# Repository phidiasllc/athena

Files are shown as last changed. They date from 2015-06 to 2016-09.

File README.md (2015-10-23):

<h1>Athena is a robot that makes lots of things</h1>
<p> Athena is derived from the <a href="https://github.com/mtu-most/most-delta">MOST Delta RepRap 3D printer</a>, which was derived from the <a href="http://www.thingiverse.com/thing:17175">Rostock RepRap 3-D Printer</a>.

<h2>SCAD files now available</h2>
In order to use the OpenSCAD files, copy them into a folder along with all of the scad files in the <a href="https://github.com/phidiasllc/scad_libraries">scad_libraries</a> repository. Render parts or plates using athena_renderer.scad.

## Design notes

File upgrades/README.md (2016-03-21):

<h1>Installing Upgrades</h1>
Upgrading requires a USB thumbdrive:
<ol>
<li>Connect a USB thumbdrive to your computer</li>
<li>Download the file(s) to install to the root of your thumbdrive.</li>
<ol>
<li>Click on the desired file in the above list</li>
<li>In right-click the button labled "Raw" in the page and select "Save link as..."</li>
<li>navigate to the location you wish to store the file</li>
</ol>
<li>Remove the thumbdrive from your computer (Eject/unmount first!)</li>
<li>Shutdown the printer and unplug power</li>
<li>Insert the thumbdrive with the downloaded files on it into the USB socket on the printer</li>
<li>Restore power to the printer</li>
<li>The beaglebone should boot, run the script and then power back down</li>
<li>After the Beaglebone has booted and then shut back down, unplug power from the printer and remove the USB thumbdrive from the USB socket in the printer</li>
<li>Restore printer power</li>
</ol>

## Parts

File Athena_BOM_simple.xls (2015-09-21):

Function | Type | Item | Count | Length | Purpose
Motor end | fastener | M3×12 socket head cap screw | 12 |  | mounting motor
Motor end | fastener | M3 washer | 18 |  | mounting motor and bar clamp
Motor end | electronic | NEMA17 motor | 3 |  | motor
Motor end | printed | Motor end | 3 |  | apex
Motor end | printed | Bar Clamp | 6 |  | clamping guide rods
Motor end | fastener | M3×16 socket head cap screw | 6 |  | Bar clamp
Motor end | fastener | M3 nut | 6 |  | Bar clamp
Motor end | fastener | #6×¾" sheet metal screw | 24 |  | apex to linking board and base
Motor end | misc | 16 tooth GT2 pulley | 3 |  | pulley
Motor end | fastener | M3×6 set screw | 6 |  | pulley set screw
Idler end | printed | Idler end | 3
Idler end | bearing | 608ZZ bearing | 6 |  | belt idler
Idler end | fastener | M8×40 hex head cap screw | 3 |  | idler shaft
Idler end | fastener | M8 nut | 3 |  | idler shaft
Idler end | fastener | M8 washer | 9 |  | idler shaft
Idler end | printed | Bar Clamp | 6 |  | clamping guide rods
Idler end | fastener | M3×16 socket head cap screw | 6 |  | Bar clamp
Idler end | fastener | M3 nut | 6 |  | Bar clamp
Idler end | fastener | M3 washer | 6 |  | Bar clamp
Idler end | fastener | #6×¾" sheet metal screw | 24 |  | apex to linking board and top
Carriages + Effector | printed | Simple Carriage | 3
Carriages + Effector | printed | Print Effector | 1
Carriages + Effector | misc | ⅜"×⅛" Counter sunk ring magnet N52 | 12
Carriages + Effector | fastener | M3×12 socket head cap screw | 3 |  | limit switch engage adjust
Carriages + Effector | fastener | M3×16 socket head cap screw | 3 |  | belt terminator
Carriages + Effector | fastener | M3 nut | 3 |  | belt terminator
Carriages + Effector | fastener | M3 washer | 3 |  | belt terminator
Carriages + Effector | printed | Fixed belt terminator | 3
Carriages + Effector | printed | Free belt terminator | 3
Carriages + Effector | misc | Small wire tie | 12 |  | bearings on carriage, belt behind terminator
Carriages + Effector | misc | Large wire tie | 3 |  | belt terminator
Carriages + Effector | misc | 6mm GT2 belt, 1500mm | 3 | 1500
Carriages + Effector | bearing | ⅜" G25 ball bearing | 12 |  | tie rod ends
Carriages + Effector | misc | 0.25"od 0.014" wall thickness 242mm aluminum rod | 6 |  | tie rods
Carriages + Effector | bearing | LM8UU linear bearing | 6 |  | Carriage
Carriages + Effector | electronic | J-head hot end (incl. 100kΩ thermistor and 5.6Ω resistor) | 1
Carriages + Effector | electronic | 40 mm fan | 1
Carriages + Effector | fastener | M3×12 socket head cap screw | 2 |  | Fan
Carriages + Effector | fastener | 4mm pneumatic quick release, drilled | 1 |  | hot end quick release
Carriages + Effector | electronic | 18ga Speaker wire, 1500mm | 1 | 1500 | heating power
Carriages + Effector | electronic | Twisted pair wire, 1500mm | 2 | 1500 | Fan and thermistor
Frame | misc | 38×210×12mm plywood | 3 |  | top linking boards
Frame | misc | 38×240×12mm plywood | 3 |  | bottom linking boards
Frame | misc | Hexagonal plywood donut | 1 |  | top
Frame | misc | Hexagonal base | 1 |  | bottom
Frame | misc | 60×605×12mm plywood | 3 |  | vertical boards (only 2 for fixed tool mount)
Frame | bearing | 8mm diameter A2 tool steel, 590mm | 6 | 590 | guide rods
Frame | fastener | M3×50 socket head cap screw | 12 |  | vertical board to apex (only 8 for fixed tool mount)
Frame | fastener | M3 nut | 12 |  | vertical board to apex (only 8 for fixed tool mount)
Frame | fastener | M3 washer | 24 |  | vertical board to apex
Electronics | fastener | M2×12 socket head cap screw | 6 |  | top limit switch
Electronics | fastener | M2 washer | 6 |  | top limit switch
Electronics | electronic | Lever action limit switch | 3 |  | top apex
Electronics | electronic | Twisted pair wire, 1500mm | 3 | 1500 | top limit switches
Electronics | electronic | Melzi controller | 1
Electronics | electronic | Beaglebone Black | 1
Electronics | printed | Electronics mount 1 | 1
Electronics | printed | Electronics mount 2 | 1
Electronics | fastener | M3×6 socket head cap screw | 7 |  | Electronics mounting
Electronics | fastener | #6×½" sheet metal screw | 3 |  | electronics mount
Electronics | electronic | rj45 extension | 1 |  | Extend BBB network connection
Electronics | electronic | USB extension | 1 |  | Extend BBB USB connection
Electronics | printed | Socket Panel | 1 |  | Panel for electrical connectors
Electronics | electronic | 5×2.5mm barrel connector | 1 |  | power input
Electronics | electronic | 18ga Speaker wire, 250mm | 1 | 250 | power input
Electronics | electronic | 18ga Speaker wire, 100mm | 1 | 100 | power input
Electronics | electronic | Melzi to beaglebone bridge board | 1 |  | BBB power
Electronics | electronic | USB cable A to mini B | 1 |  | melzi
Electronics | electronic | Heatshrink tubing | 2
Electronics | electronic | 12V 5/6A power supply | 1 |  | power
Electronics | fastener | M3×6 socket head cap screw | 2 |  | rj45 extension cord mount
Extruder drive | electronic | NEMA17 motor | 1 |  | Cold end drive
Extruder drive | misc | MK7 drive gear | 1 |  | Cold end drive
Extruder drive | fastener | M3×6 set screw | 1 |  | Drive gear
Extruder drive | bearing | MR105Z roller bearing | 1 |  | cold end shaft
Extruder drive | bearing | 608ZZ bearing | 1 |  | Cold end preload idler
Extruder drive | fastener | M3×6 socket head cap screw | 1 |  | motor mount
Extruder drive | fastener | M3×25 socket head cap screw | 1 |  | motor mount
Extruder drive | fastener | M3×30 socket head cap screw | 2 |  | motor mount
Extruder drive | misc | ¼" fuel line, 25mm | 1 | 25 | idler spring
Extruder drive | fastener | M3×45 socket head cap screw | 2 |  | idler preload
Extruder drive | fastener | M3 nut | 2 |  | idler preload
Extruder drive | fastener | M3 washer | 2 |  | idler preload
Extruder drive | fastener | #6×½" sheet metal screw | 2 |  | cold end mount
Extruder drive | misc | 2mm id 4mm od PTFE tube, 630mm | 1 | 630 | bowden sheath
Extruder drive | misc | 2mm id 4mm od PTFE tube, 40mm | 1 | 40 | infeed
Extruder drive | printed | Extruder drive body | 1 |  | cold end
Extruder drive | printed | Extruder linking bar | 1 |  | cold end
Extruder drive | printed | Extruder preload idler housing | 1 |  | cold end
Extruder drive | printed | Extruder preload idler shaft | 1 |  | cold end
Extruder drive | fastener | 4mm pneumatic quick release | 1 |  | Bowden sheath retainer
Frame | printed | Spool holder pivot | 1 |  | spool holder
Frame | printed | Spool holder arm | 1 |  | spool holder
Frame | printed | Spool holder arm retainer | 1 |  | spool holder
Frame | fastener | #6×½" sheet metal screw | 2 |  | spool holder
Frame | fastener | M3×12 socket head cap screw | 1 |  | spool holder pivot
Frame | printed | glass hold down | 3 |  | securing glass
Frame | fastener | #6×½" sheet metal screw | 3 |  | securing glass
Frame | misc | 300mm diameter glass build platform | 1

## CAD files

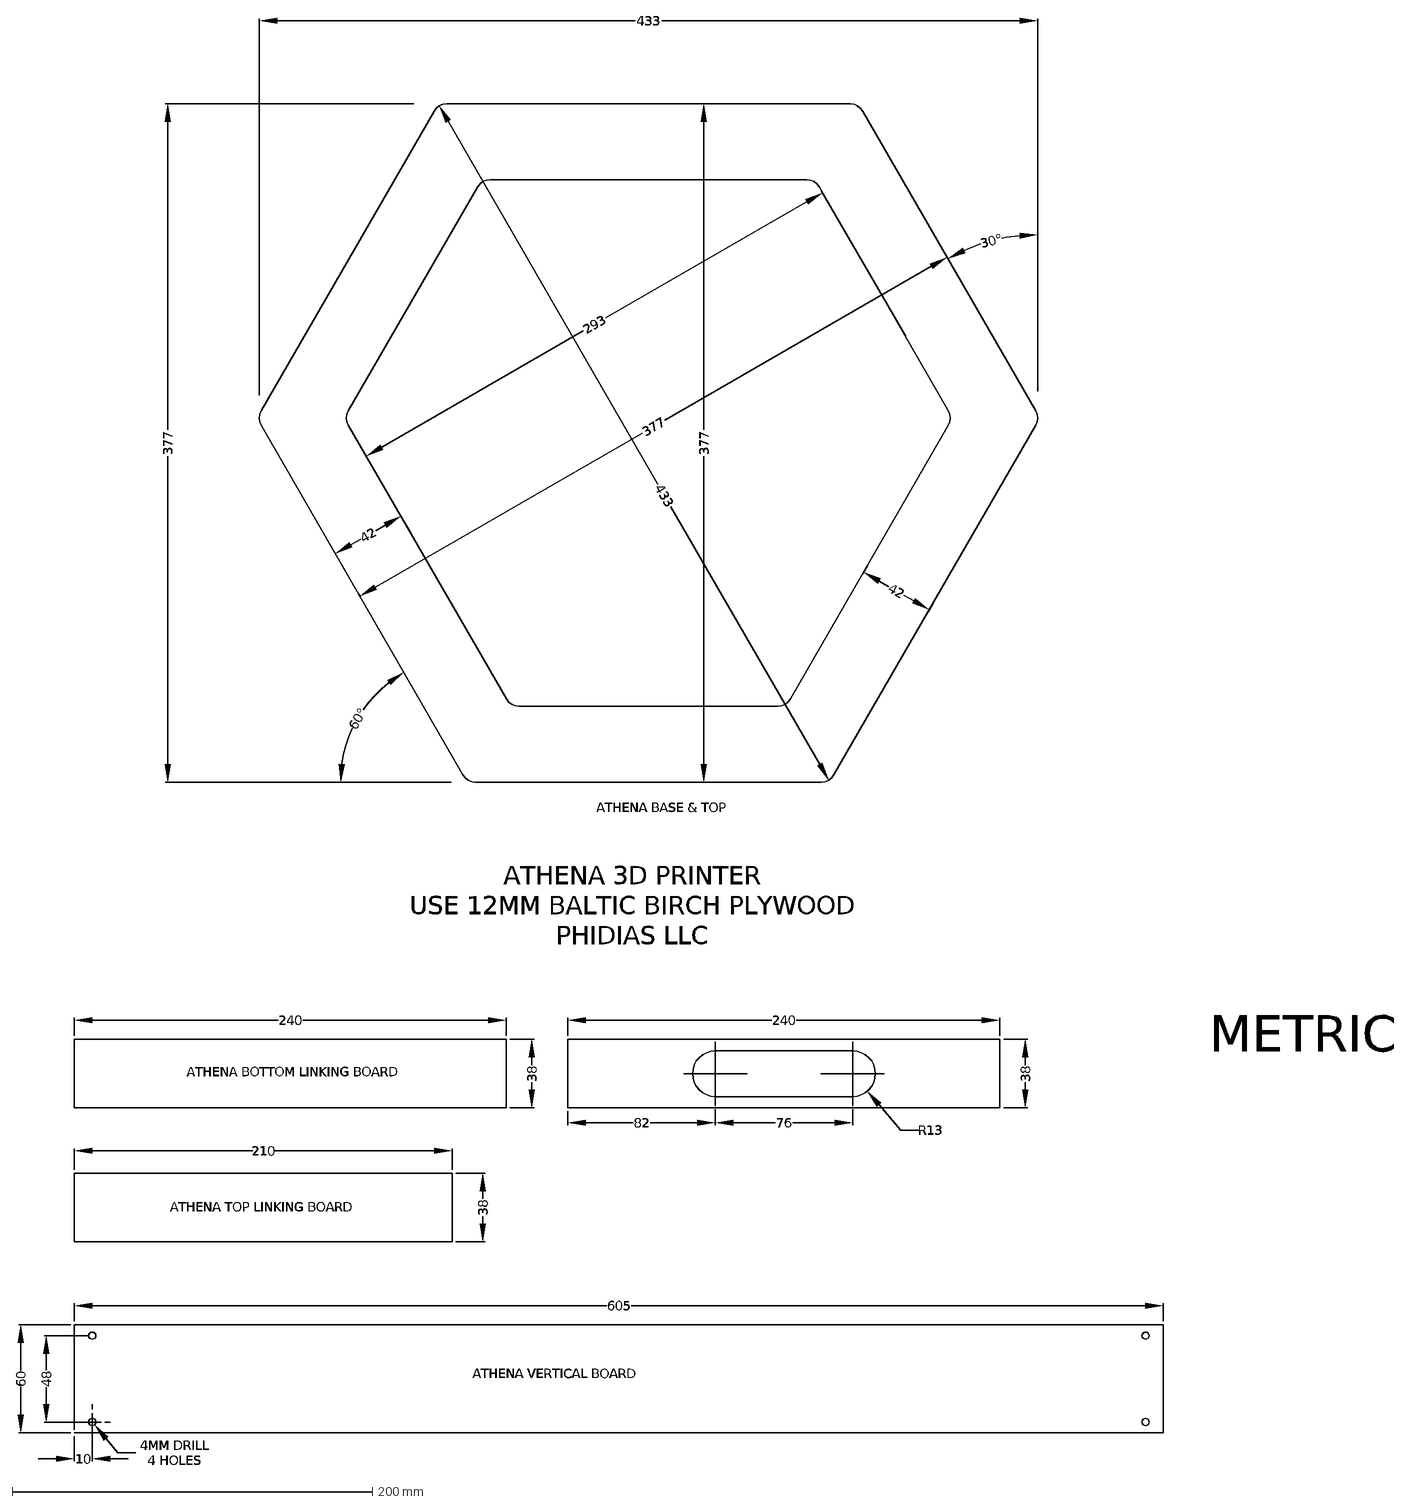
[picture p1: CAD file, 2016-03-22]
cad/ATHENA WOOD PARTS.dxf
ATHENA BOTTOM LINKING BOARD
240
38
210
ATHENA TOP LINKING BOARD
605
ATHENA VERTICAL BOARD
377
433
ATHENA BASE & TOP
42
293
82
76
R13
60
10
48
4MM DRILL 4 HOLES
60°
30°
METRIC
ATHENA 3D PRINTER USE 12MM BALTIC BIRCH PLYWOOD PHIDIAS LLC

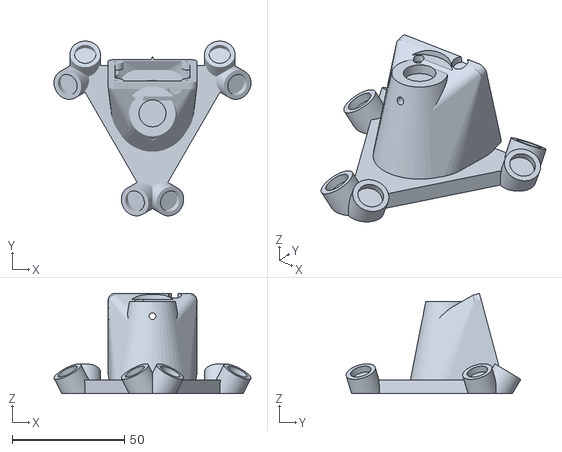
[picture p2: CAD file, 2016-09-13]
stl/hotend_effector.stl
87.9 x 77.9 x 44.7

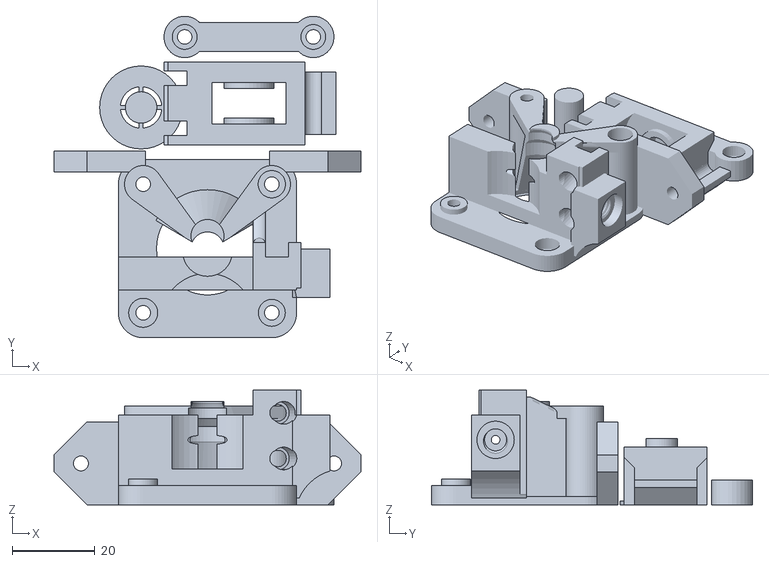
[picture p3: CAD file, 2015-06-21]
stl/extruder_drive_quickrelease.stl
74.0 x 77.5 x 27.7

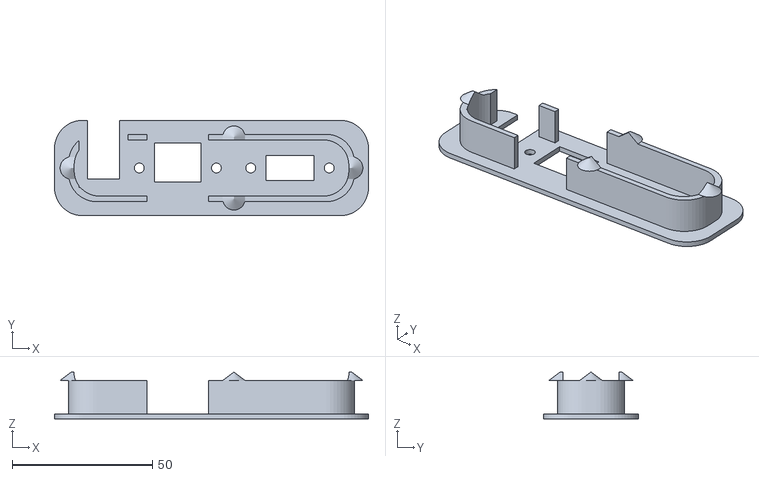
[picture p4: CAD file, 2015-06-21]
stl/connector_plate.stl
112.0 x 34.0 x 16.8

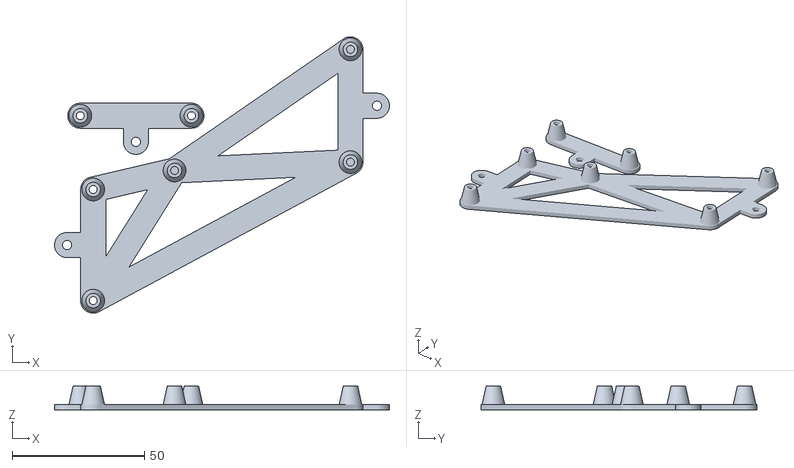
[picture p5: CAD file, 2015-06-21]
stl/electronics_mounts.stl
126.6 x 104.5 x 9.00

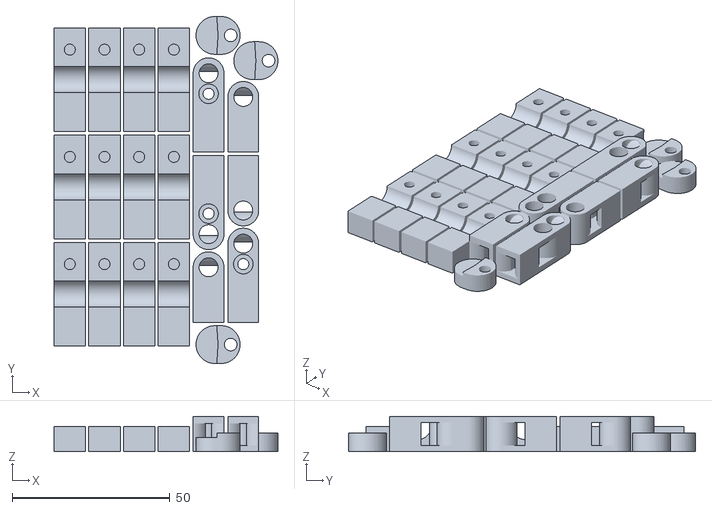
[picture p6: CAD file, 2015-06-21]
stl/bar_clamps_terms_glass_holddowns.stl
71.0 x 110.0 x 11.2

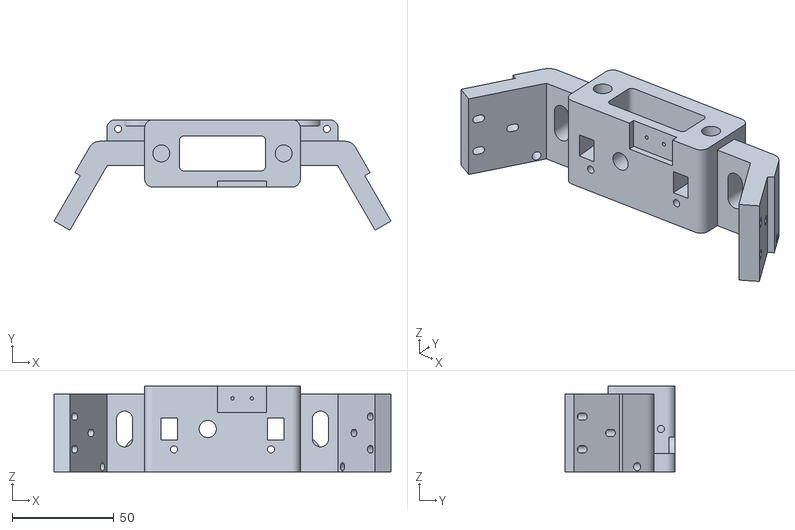
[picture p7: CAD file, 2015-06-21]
stl/end_idler.stl
165.2 x 54.1 x 42.0

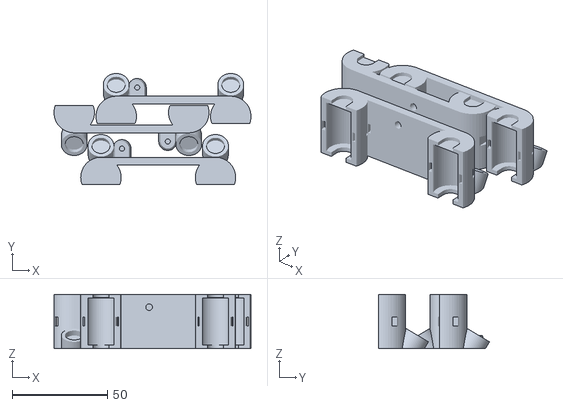
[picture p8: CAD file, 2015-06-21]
stl/simple_carriages.stl
103.2 x 58.2 x 28.5

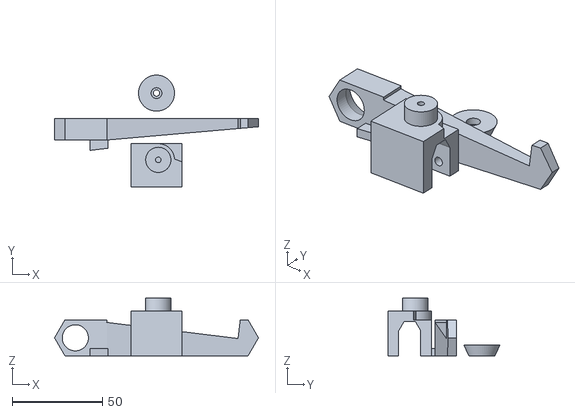
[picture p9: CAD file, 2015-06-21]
stl/spool_holder_wood.stl
113.1 x 62.0 x 32.0

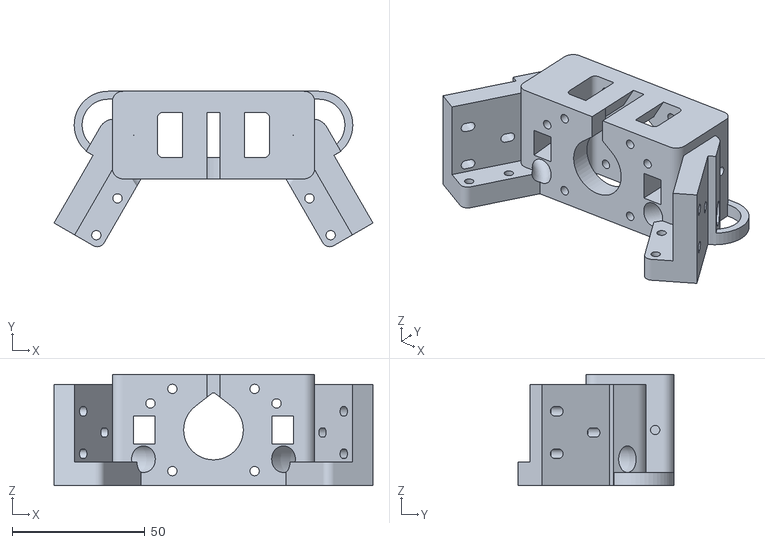
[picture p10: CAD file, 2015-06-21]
stl/end_motor.stl
120.2 x 58.6 x 42.0

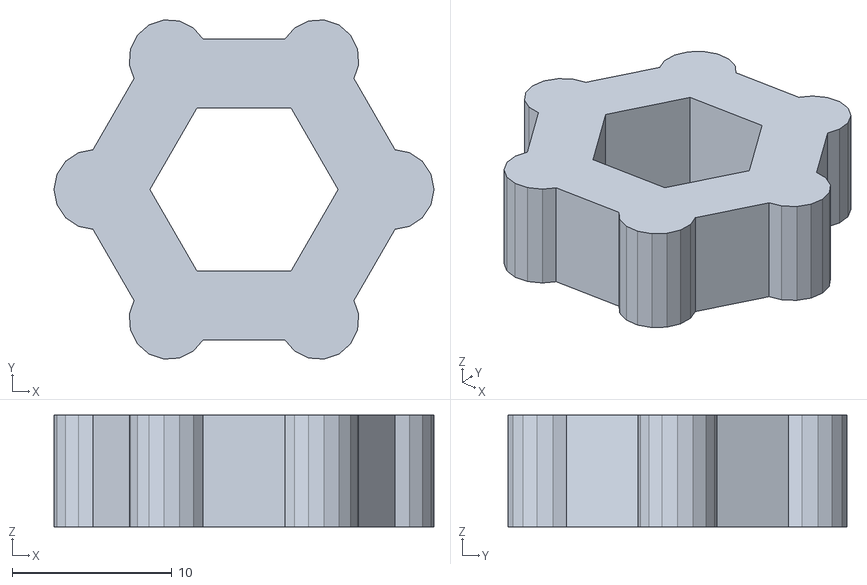
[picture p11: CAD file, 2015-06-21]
stl/thumbscrew.stl
23.8 x 21.2 x 7.00

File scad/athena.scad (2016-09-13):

/************************************************************************************

athena.scad - structural and tool objects required to build an Athena delta platform
Copyright 2015 Jerry Anzalone
Author: Jerry Anzalone <info@phidiasllc.com>

This program is free software: you can redistribute it and/or modify
it under the terms of the GNU Affero General Public License as
published by the Free Software Foundation, either version 3 of the
License, or (at your option) any later version.

This program is distributed in the hope that it will be useful,
but WITHOUT ANY WARRANTY; without even the implied warranty of
MERCHANTABILITY or FITNESS FOR A PARTICULAR PURPOSE. See the
GNU Affero General Public License for more details.

You should have received a copy of the GNU Affero General Public License
along with this program. If not, see <http://www.gnu.org/licenses/>.

************************************************************************************/

// requires the common delta modules
include <simple_delta_common.scad>

/************  layer_height is important - set it to the intended print layer height  ************/
layer_height = 0.33; // layer height that the print will be produced with

// Bowden sheath dims
d_175_sheath = 4.8;
175_bowden = [d_M4_nut, h_M4_nut, d_175_sheath];
d_300_sheath = 6.55;
300_bowden = [d_M6_nut, h_M6_nut, d_300_sheath];

bowden = 175_bowden; // set to the diameter of the Bowden sheath desired, defined above

echo_dims = false; // set to true to echo pertinent dimensions - will repeat some

// [w, l, t] = [y, x, z]
$fn = 48;
pi = 3.1415926535897932384626433832795;

// bar clamp dims
t_bar_clamp = 8;
h_bar_clamp = 10;

// the following sets the spacing of the linking board mounts on motor/idler ends
cc_idler_mounts = 120; // c-c of mounts on idler end - large to maximize x-y translation when in fixed tool mode and minimizes material use for bases
cc_motor_mounts = 75; // c-c of mounts on idler end

// printer dims
r_printer = 175; // radius of the printer, distance from printer center to guide rod centers - typically 175
l_tie_rod = 250; // length of the tie rods - typically 250
l_guide_rods = 595; // length of the guide rods - only used for assembly

// belt, pulley and idler dims
idler = bearing_608;
w_belt = 6; // width of the belt (not used)
pulley_cogs = 16; // number of cogs on the pulley
belt = GT2; // the type of drive belt to be used
h_idler_washer = h_M8_washer; // idler bearing shaft washer
d_idler_shaft_head = d_M8_nut; // idler bearing shaft head diameter
h_idler_shaft_head = h_M8_nut; // idler bearing shaft head height - sets nut pocket depth

// the diameter of the pulley isn't the whole story - the belt rides on the pulley at it's root radius
// but on the idler bearing, it rides on the tips of the cogs, pushing its pitch radius outwards
od_idler = idler[0]; // idler OD
id_idler = idler[1]; // idler id
h_idler = h_608; // thickness of idler
n_idlers = 2; // number of idler bearings
d_pulley = pulley_cogs * belt[0] / pi - (belt[1] - belt[2]); // diameter of the pulley (used to center idler)
offset_idler = (od_idler - d_pulley) / 2 + belt[2]; // amount to offset idler bearing so belt stays parallel with guide rods

// guide rod and clamp dims
cc_guides = 60; // center-to-center of the guide rods
d_guides = 8.3; // diameter of the guide rods - a little big for clearance
pad_clamp = 8; // additional material around guide rods
gap_clamp = 2; // opening for clamp

// following for tabs on either side of clamp to which linking boards are attached
// the radius of the delta measured from the center of the guide rods to the center of the triangle
// as drawn here, the tangent is parallel to the x-axis and the guide rod centers lie on y=0
//cc_mount = 75; // center to center distance of linking board mount pivot points standard = 75
h_apex = 1.5 * 25.4; // height of the portion of motor and idler ends mating with linking board
w_mount = 12; // thickness of the tabs the boards making up the triangle sides will attach to
l_mount = 40; // length of said tabs
cc_mount_holes = 16;
l_base_mount = l_mount;
w_base_mount = 14.1;
t_base_mount = 9.0;
r_base_mount = 3;
l_mount_slot = 2; // length of the slot for mounting screw holes

cc_v_board_mounts = 2 * (cc_guides / 2 - pad_clamp + d_M3_screw / 2); // c-c mounts for vertical boards

l_idler_relief = cc_guides - d_guides - pad_clamp - 1.5; // with guide rod clamp design, the length needs to be smaller so there are walls for bridging
w_idler_relief = n_idlers * h_idler + 2 * h_idler_washer;
r_idler_relief = 2; // radius of the relief inside the apex
l_clamp = cc_guides + d_guides + pad_clamp;
w_clamp = w_idler_relief + pad_clamp + 8;
h_clamp = l_NEMA17;

// magnetic ball joint dims
d_ball_bearing = 3 * 25.4 / 8;
id_magnet = 15 * 25.4 / 64;
od_magnet = 3 * 25.4 / 8;
h_magnet = 25.4 / 8;
r_bearing_seated = pow(pow(d_ball_bearing / 2, 2) - pow(id_magnet / 2, 2), 0.5); // depth ball bearing sinks into magnet id
h_carriage_magnet_mount = 9;
h_effector_magnet_mount = 10;
r_pad_carriage_magnet_mount = 2;
r_pad_effector_magnet_mount = 2;

// effector dims
// l_effector needs to be played with to keep the fan from hitting the tie rods
l_effector = 60; // cc of tie rod bearings on effector
h_effector = equilateral_height_from_base(l_effector);
r_effector = l_effector * tan(30) / 2 + 11; // radius of the magnet mounts
t_effector = 6; // thickness of the effector base
h_triangle_inner = h_effector + 12;
r_triangle_middle = equilateral_base_from_height(h_triangle_inner) * tan(30) / 2;

// for the small tool end effector:
d_small_effector_tool_mount = 30; // diameter of the opening in the end effector that the tool will pass through
d_small_effector_tool_magnet_mount = 1 + d_small_effector_tool_mount + od_magnet + 2 * r_pad_effector_magnet_mount; // ring diameter of the effector tool magnet mounts

// for the large tool end effector:
d_large_effector_tool_mount = 50;
d_large_effector_tool_magnet_mount = h_triangle_inner;

// Bowden sheath quick release fitting dims
d_quickrelease_threads = 6.4; // M6 threads, but this gives best fit
l_quickrelease_threads = 5; // length of threads on quick release
pitch_quickrelease_threads = 1;
d_quickrelease = 12; // diameter of the hex portion for counter-sinking quick release into hot end tool
countersink_quickrelease = 6; // depth to contersink quick release fitting into hot end tool when not headless

// hot end dims
pad_jhead = 8; // this is added to the diameter of the cage to permit clearance for the hotend
pad_e3d = 14;
t_hotend_cage = t_heat_x_jhead - h_groove_jhead - h_groove_offset_jhead;
d_hotend_side = d_large_jhead + pad_jhead;
z_offset_retainer = t_hotend_cage - t_effector / 2 - 3;  // need an additional 3mm to clear the interior of the cage
a_fan_mount = 15;
l_fan = 39.5;
r_flare = 6;
h_retainer_body = h_groove_jhead + h_groove_offset_jhead + 4;
r1_retainer_body = d_hotend_side / 2 + r_flare * 3 / t_hotend_cage;
r2_retainer_body = r1_retainer_body - r_flare * h_retainer_body / t_hotend_cage;
r2_opening = (d_hotend_side - 5 ) / 2 + r_flare * (t_hotend_cage - 6 - t_effector + 3.0) / (t_hotend_cage - 6);//r1_opening - r_flare * (t_effector + 1.5) / t_hotend_cage;
r1_opening = r2_opening - 1.5;
d_retainer_screw = d_M2_screw;

// carriage dims:
w_carriage_web = 4;
h_carriage = l_lm8uu + 4;
carriage_offset = 18.6; // distance from center of guide rods to center of ball mount pivot
y_web = - od_lm8uu / 2 - (3 - w_carriage_web / 2);
stage_mount_pad = 2.2;

// limit switch dims
l_limit_switch = 24;
w_limit_switch = 6;
t_limit_switch = 14;
cc_limit_mounts = 9.5;
limit_x_offset = 11; // 11 places limit switch at guide rod, otherwise center at cc_guides / 2 - 8
limit_y_offset = d_M3_screw - carriage_offset;

// center-to-center of tie rod pivots
tie_rod_angle = acos((r_printer - r_effector - carriage_offset) / l_tie_rod);

// tool mount member dims
w_member = 25.4; // narrow dimension of member
l_member = 3 * 25.4; // wide dimension of member

// aluminum member dims
l_vertical_board = 3 * 25.4; // long dimension of rectangular tube making vertical board
w_vertical_board = 25.4; // short dimention of rectangular tube making vertical board
l_linking_board = 38.6;
w_linking_board = 3 * 25.4 / 4;

// BBB dims; origin at corner w/ power jack, starting from hole nearest power jack, going counter clockwise
bbb_hole0 = [14.61, 3.18];
bbb_hole1 = [14.61 + 66.5, 6.35];
bbb_hole2 = [14.61 + 66.5, 6.35 + 42.6];
bbb_hole3 = [14.61, 3.18 + 48.39];
bbb_holes = [bbb_hole0, bbb_hole1, bbb_hole2, bbb_hole3];
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

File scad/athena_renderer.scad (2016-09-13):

/************************************************************************************

athena_renderer.scad - easily select and render parts and plates for manufacture of Athena platform
Copyright 2015 Jerry Anzalone
Author: Jerry Anzalone <info@phidiasllc.com>

This program is free software: you can redistribute it and/or modify
it under the terms of the GNU Affero General Public License as
published by the Free Software Foundation, either version 3 of the
License, or (at your option) any later version.

This program is distributed in the hope that it will be useful,
but WITHOUT ANY WARRANTY; without even the implied warranty of
MERCHANTABILITY or FITNESS FOR A PARTICULAR PURPOSE. See the
GNU Affero General Public License for more details.

You should have received a copy of the GNU Affero General Public License
along with this program. If not, see <http://www.gnu.org/licenses/>.

************************************************************************************/

// include the modules required for rendering
include <athena.scad>

render_part(part_to_render = 14);
//render_plate(plate_to_render = 1);

// renders individual parts
module render_part(part_to_render) {
	// end that holds motor - 3 required
	if (part_to_render == 1) athena_end_idler(z_offset_guides = 8);

	// end that holds idler bearings and end limit switches - 3 required
	if (part_to_render == 2) athena_end_motor(z_offset_guides = 8);

	// clamps the guide rods firmly to motor/idler ends - 12 required
	if (part_to_render == 3) bar_clamp();

	// permits tensioning of belts and mount point to carriage - 3 sets required
	if (part_to_render == 4) athena_belt_terminators();

	// carriages ride on the guide rods 3 required for basic platform
	if (part_to_render == 5) athena_basic_carriage();

	// carriages ride on the guide rods 3 required for Parthenos
	if (part_to_render == 6) athena_convertible_carriage(linear_bearing = bearing_lm8uu);

	// the roller switch mount - 3 required for Parthenos
	if (part_to_render == 7) central_limit_switch();

	// if the platform uses a BBB and melzi, one of these is required
	if (part_to_render == 8) bbb_melzi_mount(render_large = true, render_small = true);

	// mounts to vertical board, holds magnetic tools not in use and hides wires - convenience, not required for Parthenos
	if (part_to_render == 9) athena_tool_holder();

	// mounts to vertical board to which extruder drive is mounted and holds spool - convenience, not required
	if (part_to_render == 10) athena_spool_holder(render_mount = true, render_holder = false
	, mount_wood = true);

	// mounts to vertical board, holds tools and hides wires - convenience, not required
	if (part_to_render == 11) athena_hand_tool_holder(wood_mount = true, sonicare_magnet = false);

	// Mounting plate fits in slotted motor-end linking board, one required; print with support
	if (part_to_render == 12) connector_plate();

	// for holding glass to base plate, three required
	if (part_to_render == 13) glass_holddown();

	// end effector with built-in mount for hot end, one required for basic platform
	if (part_to_render == 14) hotend_effector(headless = true, quickrelease = true, vent = false, dalekify = false);

	// thumbscrew for the quick release connector
	if (part_to_render == 15) thumbscrew_quickrelease();

	// shroud mounted to bottom of end effector for improved print cooling
	if (part_to_render == 16) hotend_shroud(height = 18, twist = 5);

	// a place to play
	if (part_to_render == 99) sandbox();
}

// renders production plates
module render_plate(plate_to_render) {
	// approximate build circle to assure placement and fit on build platform
//	color([1, 0, 0])
//		circle(r = 125);

	if (plate_to_render == 1)
		for (i = [-1:1])
			translate([0, i * (w_clamp + 2) + 20, 0])
				athena_end_idler(z_offset_guides = 8);

	if (plate_to_render == 2) {
		translate([0, -w_clamp / 2 - 6, 0])
			athena_end_motor();

		translate([0, w_clamp / 2 + 6, 0])
			rotate([0, 0, 180])
				athena_end_motor();

		translate([l_clamp - 6, 0, 0])
			rotate([0, 0, 90])
				athena_end_motor();
	}

	// hot end effector
	if (plate_to_render == 3) {
		hotend_effector(quickrelease = true, dalekify = false);
	}

	// fixed terminators
	if (plate_to_render == 4) {
		for (i = [-3:2], j = [-1:1])
			//rotate([0, 0, i * 120])
				translate([i * 11, j * 32, 0])
					athena_fixed_belt_terminator();
	}

	// free terminators
	if (plate_to_render == 5) {
		for (i = [-3:2], j = [-1:1])
			//rotate([0, 0, i * 120])
				translate([i * 11, j * 25, 0])
					athena_free_belt_terminator();
	}

	// bar clamps
	if (plate_to_render == 6) {
		translate([-h_bar_clamp / 2 - 6, -w_clamp - 1, t_bar_clamp / 2])
			for (i = [0:2])
				for (j = [-4:3])
					translate([j * -(h_bar_clamp + 1), i * (w_clamp + 1), 0])
						bar_clamp();
	}

	if (plate_to_render == 7) {
		// Parthenos carriages
		translate([22, -2, 0])
			rotate([0, 0, 180])
				athena_convertible_carriage();

		athena_convertible_carriage();

		translate([14, -39, 0])
			rotate([0, 0, 180])
				athena_convertible_carriage();
	}

	if (plate_to_render == 8) {
		translate([22, -2, 0])
			rotate([0, 0, 180])
				athena_basic_carriage();

		athena_basic_carriage();

		translate([14, -34, 0])
			rotate([0, 0, 180])
				athena_basic_carriage();
	}

	if (plate_to_render == 9) {
		for (i = [-1:1], j = [-2:1])
			translate([i * 19, j * 22 + ((i == 0) ? 11 : 0), 0])
				thumbscrew_quickrelease();
	}

	if (plate_to_render == 10) {
		for (i = [-1:1], j = [-1,0])
			translate([i * 30, j * 25 + 12.5, 0])
			athena_spool_holder(
				render_mount = true,
				render_holder = false,
				mount_wood = true);
	}

	if (plate_to_render == 11) {
		for(i = [-1:1])
			translate([0, i * 55, 0])
				bbb_melzi_mount(render_large = true, render_small = false);

	}
}

module sandbox() {
	linear_bearing = bearing_lm8uu;
	spacing = 0.5;
	union() {
		translate([0, 0, -h_carriage / 2 + spacing])
			difference() {
				union() {
					carriage_body(linear_bearing = linear_bearing);

					// magnet mounts
					for (i = [-1, 1])
						translate([i * l_effector / 2, -carriage_offset, stage_mount_pad + h_carriage_magnet_mount / sin(tie_rod_angle)])
							rotate([90 - tie_rod_angle, 0, 0])
								magnet_mount(r_pad = r_pad_carriage_magnet_mount, h_pad = h_carriage_magnet_mount);

					mirror([0, 0, 1])
						for (i = [-1, 1])
							translate([i * l_effector / 2, -carriage_offset, stage_mount_pad + h_carriage_magnet_mount / sin(tie_rod_angle)])
								rotate([90 - tie_rod_angle, 0, 0]) {
									magnet_mount(r_pad = r_pad_carriage_magnet_mount, h_pad = h_carriage_magnet_mount);

									// support for printing the mounts
									translate([0, 0, (h_magnet + h_carriage_magnet_mount) / 2 - r_bearing_seated + 0.25])
										difference() {
											cylinder(r = od_magnet / 2 + r_pad_carriage_magnet_mount, h = h_magnet + h_carriage_magnet_mount, center = true);

											cylinder(r = od_magnet / 2, h = h_magnet + h_carriage_magnet_mount, center = true);
										}
							}

				}

				for (i = [-1, 1])
					translate([i * cc_guides / 2, 0, 0])
						carriage_wire_tie_relief(
							linear_bearing = linear_bearing,
							clearance = 0.5
						);

				carriage_bearing_relief(linear_bearing = linear_bearing);

				// flatten the bottom
				translate([0, 0, -h_carriage])
					cube([2 * cc_guides, 4 * (linear_bearing[0] + 6), h_carriage], center = true);
			}
		// bottom half
		translate([0, 0, h_carriage / 2 - spacing])
			difference() {
				union() {
					carriage_body(limit_switch_mount = false, linear_bearing = linear_bearing);

					// add a protrusion for making the vertical board-mounted directional limit switch
					translate([d_pulley / 2 + x_pass / 2 + 5, y_web - 7.5, 0]) // offset it from the belt terminator mount point
						rotate([0, 90, 0])
							intersection() {
								cylinder(r = h_carriage / 2, h = 7, center = true);

								translate([0, h_carriage / 2 - y_web - 2, 0])
									cube([h_carriage, h_carriage, 11], center = true);
							}

				}
				for (i = [-1, 1])
					translate([i * cc_guides / 2, 0, 0])
					carriage_wire_tie_relief(
						linear_bearing = linear_bearing,
						clearance = 0.5
					);

				carriage_bearing_relief(linear_bearing = linear_bearing);

				// belt terminator mount
				translate([d_pulley / 2, y_web, h_carriage / 2 - d_M3_screw / 2 - 5])
					rotate([90, 0, 0])
						cylinder(r = d_M3_screw / 2, h = w_carriage_web + 2, center = true);
			}
	}
}

module hotend_shroud(
	height,
	twist
) {
	t_shroud_base = 2.5;
	t_shroud = 0.6;

	difference() {
		hull() {
		union() {
			cylinder(r = r1_opening + 1.5 + t_shroud, h = t_shroud_base);

				hull()
					effector_shroud_holes(diameter = d_M3_cap / 2, height = t_shroud_base);

				translate([0, 0, height - 0.1])
					cylinder(r = r1_opening + 1.5 + t_shroud, h = 0.1);
			}
		}
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

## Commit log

2015-06-20 use device, not IP, for iptables
2015-06-20 reorganize things
    [00000001_dogtoy.g]
2015-06-20 disable wicd on wired interface
2015-07-19 print actual hostname
2015-09-21 added BOM
    [Athena_BOM_simple.xls]
2015-10-16 added scad files
    [athena.scad, athena_renderer.scad]
2015-10-23 updated Bowden parameters
    [athena.scad]
2015-10-23 vented end effector
    [athena.scad, athena_renderer.scad]
2016-03-21 update for new bridge board and jessie
2016-03-21 beltcutter models and script
    [beltcutter.scad, cbox.scad]
2016-03-22 added cad for wood parts
    [ATHENA WOOD PARTS.dxf]
2016-04-09 remove beltcutter
    [beltcutter.scad, cbox.scad]
2016-09-13 updated scad and stl
    [athena.scad, athena_renderer.scad, hotend_eff_thumb.stl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]
